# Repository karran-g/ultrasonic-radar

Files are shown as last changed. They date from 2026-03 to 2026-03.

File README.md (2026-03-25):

# Ultrasonic Radar

A real-time ultrasonic radar built with an Arduino Uno, HC-SR04 sensor, and SG90 servo motor. The servo sweeps the sensor across a 150° arc while the Arduino measures distances via time-of-flight. Readings are streamed over serial to a Python/PyGame visualization displaying a live polar radar sweep.

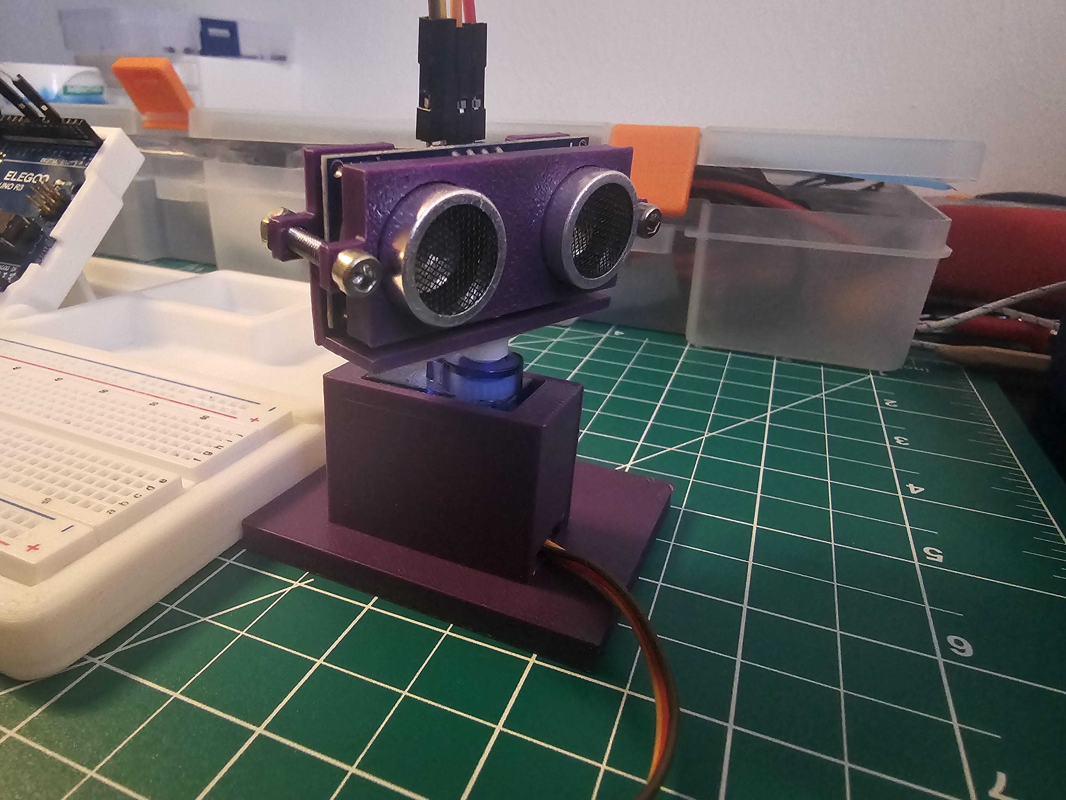
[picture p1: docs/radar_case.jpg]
Electronics Setup


---

## How It Works

The SG90 servo rotates the HC-SR04 sensor from 15° to 165° in 1° steps with a 30ms delay per step. At each angle, the sensor emits a 40kHz ultrasonic pulse and measures the time for the echo to return. The Arduino converts this to distance using the speed of sound at 15° Celsius and sends `angle,distance` pairs over serial at 9600 baud.

The Python script reads this serial stream in real time and renders a polar grid in PyGame. The sweep line is green up to the detected object and red beyond it, with a fading trail showing recent sweep history.

---

## Hardware

| Component | Quantity |
|---|---|
| Arduino Uno R3 | 1 |
| HC-SR04 Ultrasonic Sensor | 1 |
| SG90 Micro Servo | 1 |
| Breadboard Power Module (USB) | 1 |
| Breadboard | 1 |
| Jumper Wires | Several |
| M3*18 bolts and nuts | 2 |

All mechanical mounts were custom designed in Autodesk Inventor and 3D printed on a Bambu Lab A1 Mini with PLA plastic. Initially, I tried designing the sensor case so that I could mount the sensor using 4x 1.5 mm diameter pegs that could fit the 4 holes on the HC-SR04's corners;
However, this did not really work out, so I switched to a bolted design.
> **Note:** The parts are not oriented properly in the STL files so make sure to orient them properly in your slicer before printing.

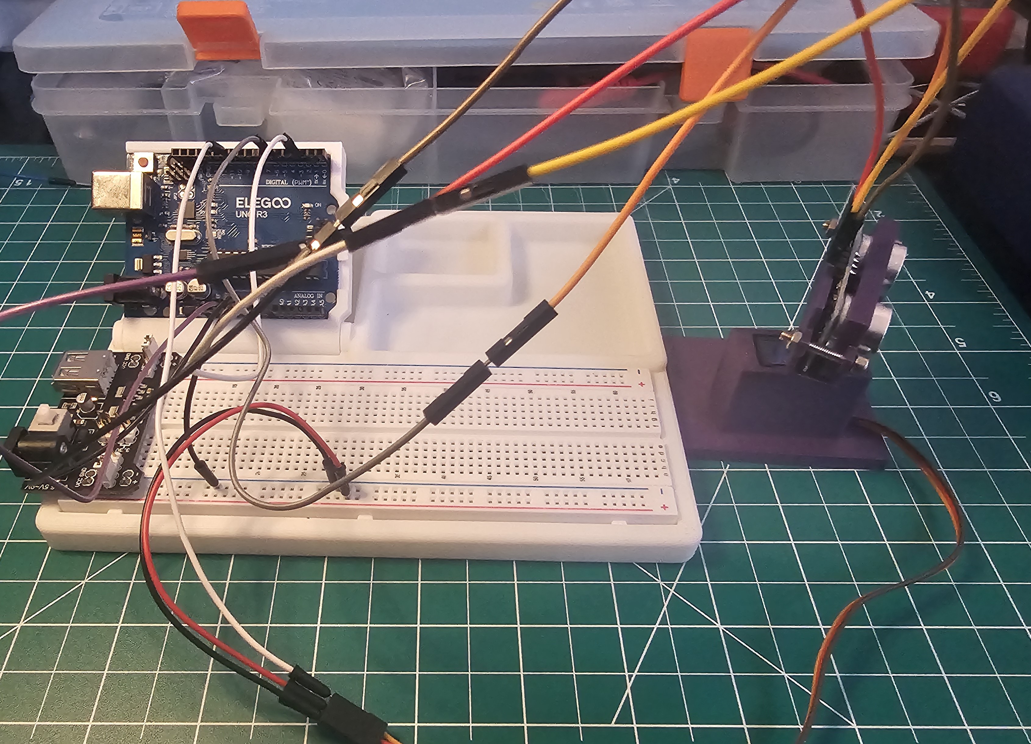
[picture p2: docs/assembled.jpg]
Sensor Mount Assembly


---

## Wiring

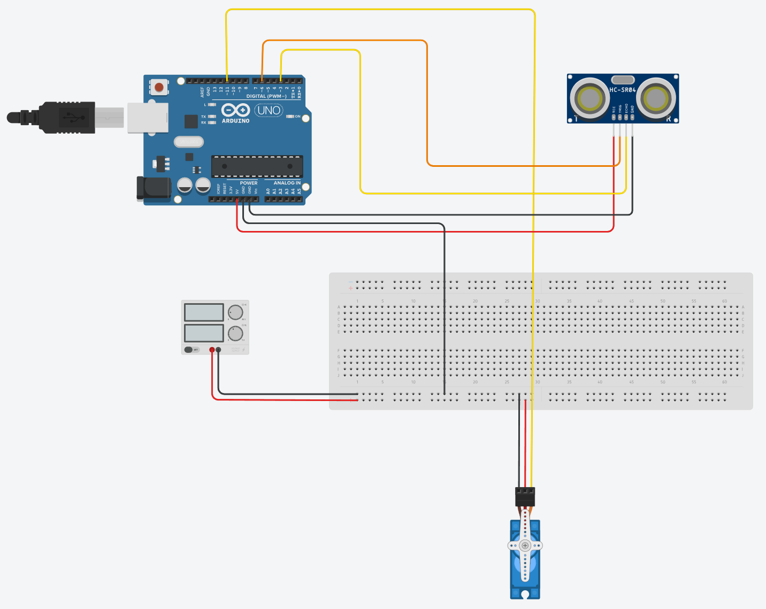
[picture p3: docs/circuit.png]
Wiring Diagram


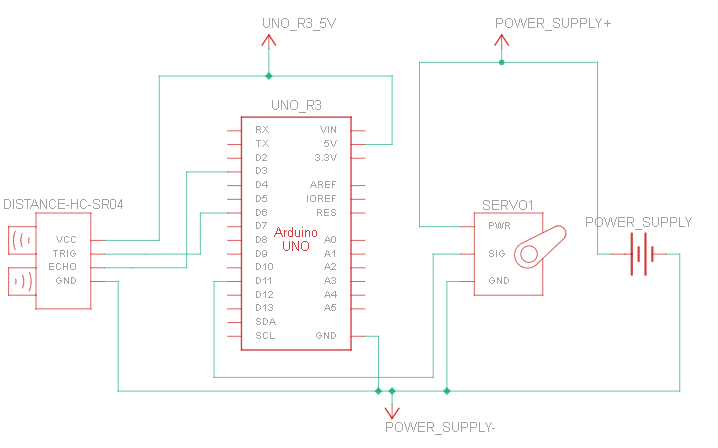
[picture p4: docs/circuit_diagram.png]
Schematic


| HC-SR04 Pin | Arduino Pin |
|---|---|
| VCC | 5V |
| TRIG | D6 |
| ECHO | D3 |
| GND | GND |

| SG90 Pin | Connection |
|---|---|
| VCC (Red) | Breadboard Power Module 5V |
| GND (Brown) | Common GND |
| Signal (Orange) | Arduino D11 |

> **Note:** The servo must be powered from the breadboard power module, not directly from the Arduino 5V pin. The Arduino cannot supply enough current for the servo under load.
> For the servo power supply, I would suggest a 9V DC battery; however, keep in mind that if the battery is almost out of juice, you can spend hours debugging only to find out that it wasn't the code but the battery. :<

---

## Demo

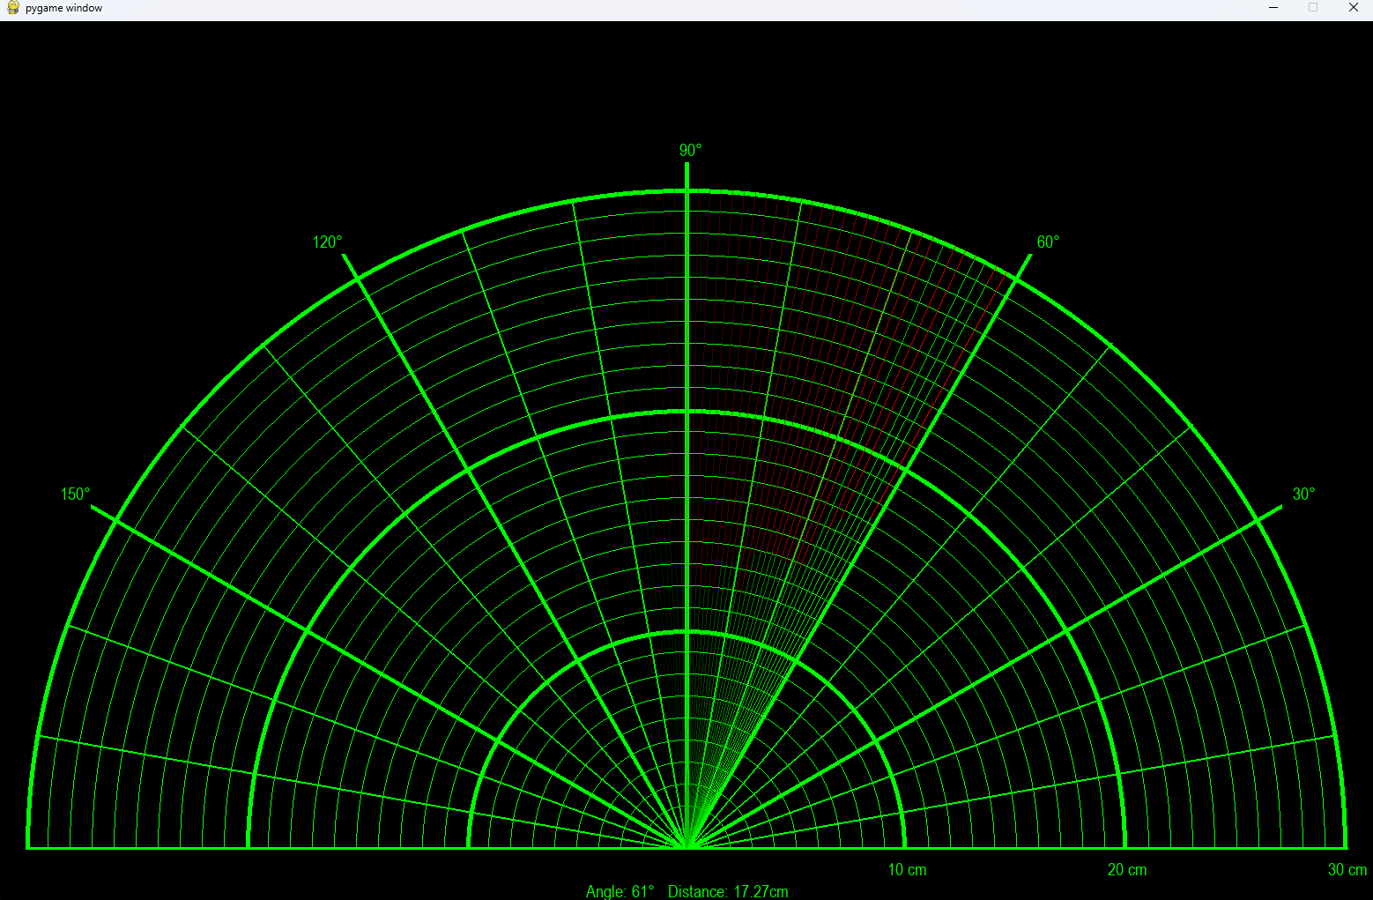
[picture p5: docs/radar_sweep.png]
Radar Visualization


---

## Software Dependencies

**Firmware**
- Arduino IDE 2.x

**Visualization**
- Python 3.x
- PyGame
- PySerial

Install Python dependencies:
```
pip install pygame pyserial
```

---

## Setup & Usage

**1. Flash the firmware**

Open `firmware/radar.ino` in Arduino IDE. All three `.ino` files (`radar.ino`, `sensor.ino`, `servo.ino`) must be in the same folder; Arduino IDE will compile them together automatically. Upload to the Arduino Uno.

**2. Configure the serial port**

Open `visualization/radar.py` and update line 3 to match your Arduino's COM port:
```python
com = 'COM4'  # Change this to your port (e.g. COM3, /dev/ttyUSB0 on Linux)
```

**3. Run the visualization**

With the Arduino connected and powered:
```
python radar.py
```

---

## Known Limitations

- Maximum detection range is 30cm. The HC-SR04 supports up to 400cm, but the sweep speed and serial throughput were tuned for short range.
- The COM port is hardcoded in `radar.py` and must be manually changed per machine.
- If no serial data is received, the visualization freezes; there is no timeout or reconnection logic.
- Measurement accuracy is approximately ±0.2cm at a 30cm distance.
- IMPORTANT: If the Arduino IDE is open at the same time you run the radar.py, you may get a serial error if the board is actively communicating with the Arduino IDE.

---

## Future Improvements

- Configurable COM port and baud rate via command line arguments instead of hardcoded values
- Serial timeout and reconnection logic to prevent visualization freezing on data loss
- Increase detection range beyond 30cm by tuning sweep speed and serial throughput
- Export scan data to CSV for offline analysis
- 3D printed enclosure to house the Arduino and breadboard as a single unit

---

## License

MIT License — see [LICENSE](LICENSE) for details.

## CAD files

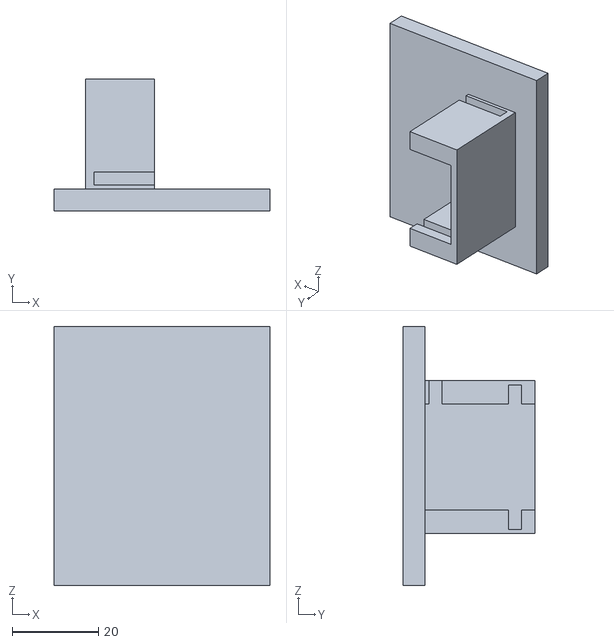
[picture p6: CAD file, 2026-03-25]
cad/servo_part1.stl
50.0 x 30.5 x 60.0

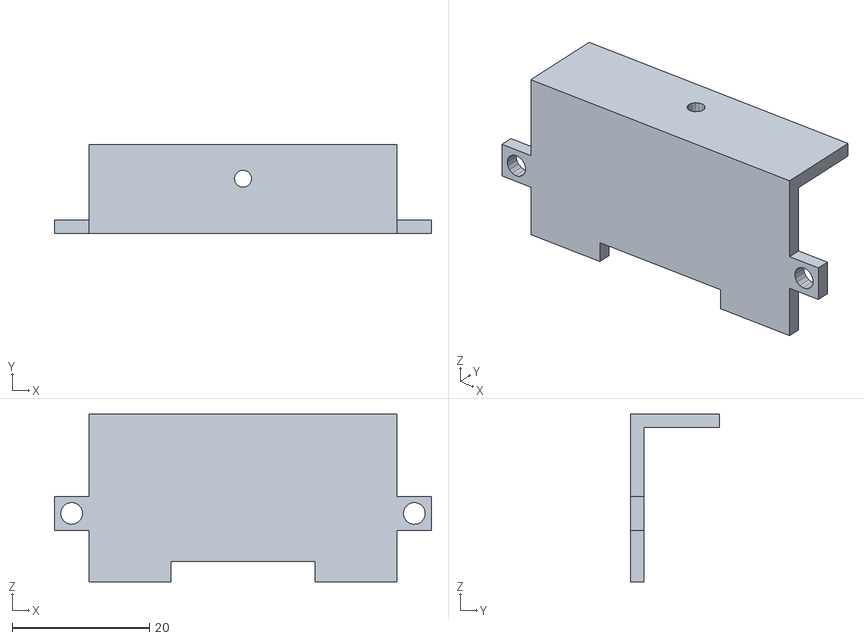
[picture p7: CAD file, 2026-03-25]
cad/Sensor_Holder.stl
55.0 x 13.0 x 24.5

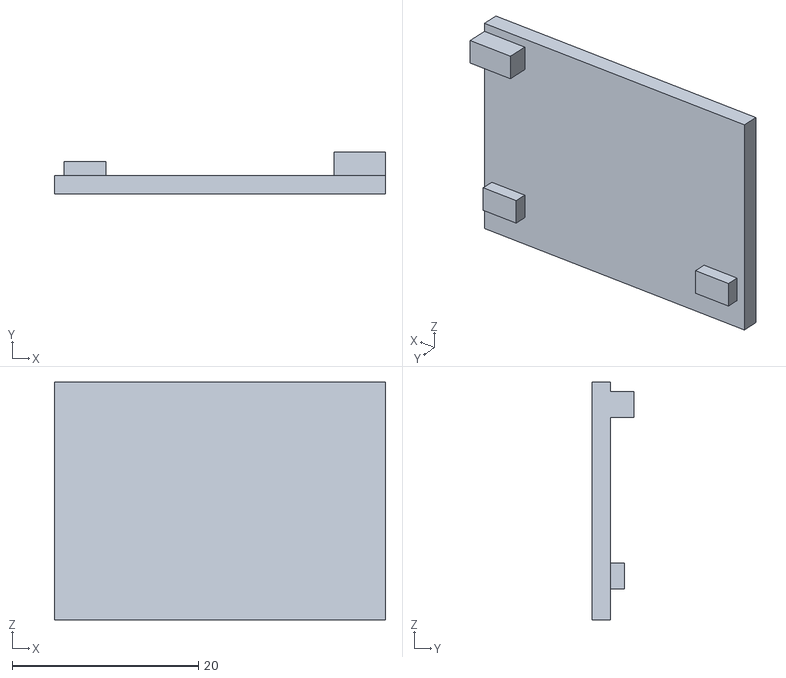
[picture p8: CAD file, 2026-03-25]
cad/servo_part2.stl
35.5 x 4.50 x 25.5

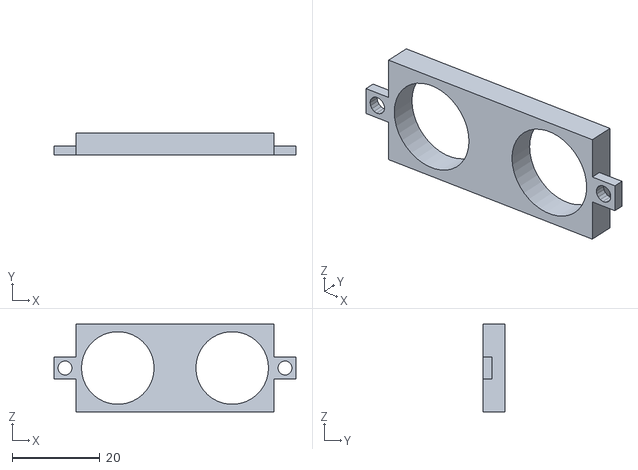
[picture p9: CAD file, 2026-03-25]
cad/sensor_Holder_part2.stl
55.0 x 5.00 x 20.0

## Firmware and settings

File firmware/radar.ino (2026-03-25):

void setup() {
  Serial.begin(9600);
  sensorInit();
  servoInit();
}
void sweep() {
  float D;  // distance variable being declared locally
  //Positive Sweep
  for (int i = 15; i <= 165; i += 1) {
    moveTo(i);
    delay(10);
    D = getDistance();
    Serial.print(i);  // Angle
    Serial.print(",");
    Serial.println(D);  // Distance
    delay(20);
  }
  //Negative sweep
  for (int i = 165; i >= 15; i -= 1) {
    moveTo(i);
    delay(10);
    D = getDistance();
    Serial.print(i);  // Angle
    Serial.print(",");
    Serial.println(D);  // Distance
    delay(20);
  }
}

void loop() {
  sweep();
}

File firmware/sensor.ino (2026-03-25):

const int TRIG = 6;
const int ECHO = 3;
const long timeout = 30000;
const float V_sound = 0.0340;  // cm/uS at 15 deg C
const float Max_range = 30;
const float Error_code = 5000000.0;

// Sensor initialization
void sensorInit() {

  pinMode(TRIG, OUTPUT);
  pinMode(ECHO, INPUT);

  // Set Trig low by default
  digitalWrite(TRIG, 0);
}
// Echo measure
long measureEcho(long timeout) {
  long delayTime_start = micros();
  while (digitalRead(ECHO) == LOW) {
    if ((micros() - delayTime_start) > timeout) {
      // This means that the echo has been Low longer than the timeout and it was'nt set to high even after the Trigger, Thus something must be wrong
      return -1;  //error code
    }
  }
  // executed only if there were no issues and the delay time was less than timeout
  long t1 = micros();
  while (digitalRead(ECHO) == HIGH) {
    if ((micros() - t1) > timeout) { // if this is executed this means object was out of range and 0 (No object is returned)
      return 0;
    }
  }
  long t2 = micros();
  return (t2 - t1); //current time - time just before echo was set to high
}

// get Distance
float getDistance() {
  float d;
  // Trigger pulse
  digitalWrite(TRIG, 0);
  delayMicroseconds(2);
  digitalWrite(TRIG, 1);
  delayMicroseconds(10);
  digitalWrite(TRIG, 0);

  // Echo detection
  long t = measureEcho(timeout);
  //distance calculated
  d = (V_sound * t) / 2;
  // returns either the distance if less than the max range or just 0 
  if (t!=-1 && d < Max_range){
    return d;
  }
  return 0;
}
